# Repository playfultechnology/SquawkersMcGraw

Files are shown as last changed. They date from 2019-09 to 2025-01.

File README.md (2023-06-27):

# SquawkersMcGraw
Reverse engineering and remixing the Hasbro FurReal Friend "Squawkers McGraw" animatronic parrot
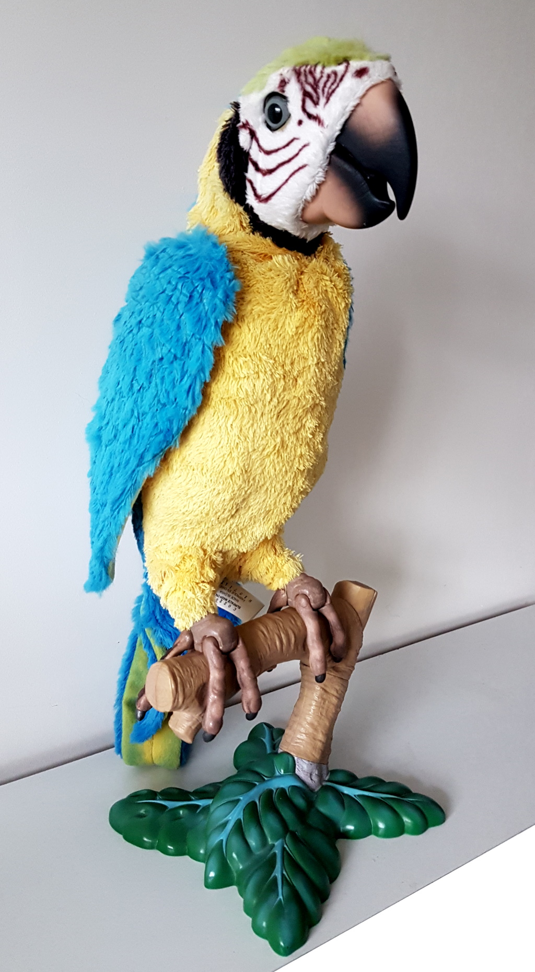
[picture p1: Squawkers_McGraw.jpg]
Squawkers McGraw Animatronic Parrot


## Internals
<table>
<tr>
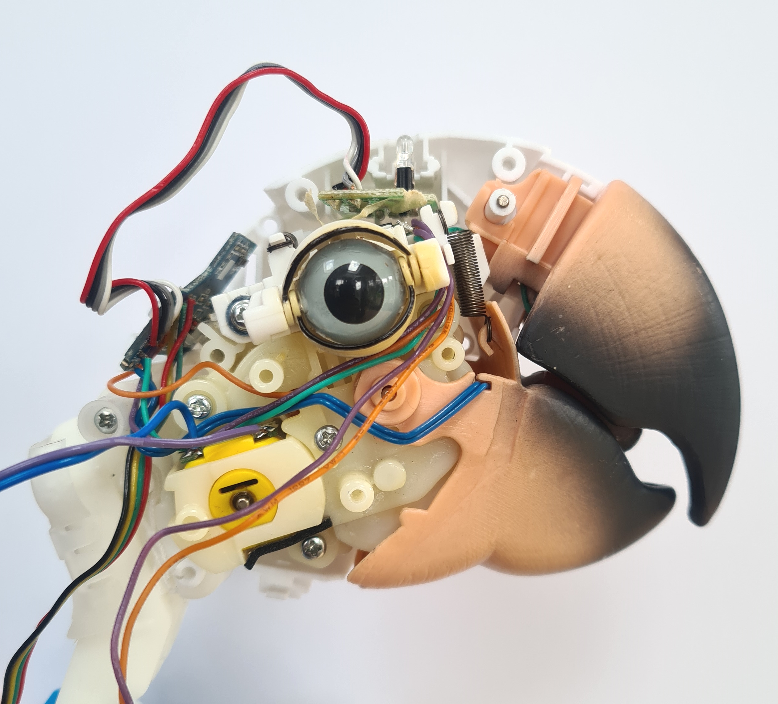
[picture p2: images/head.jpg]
Squawkers McGraw Head
<td></td>
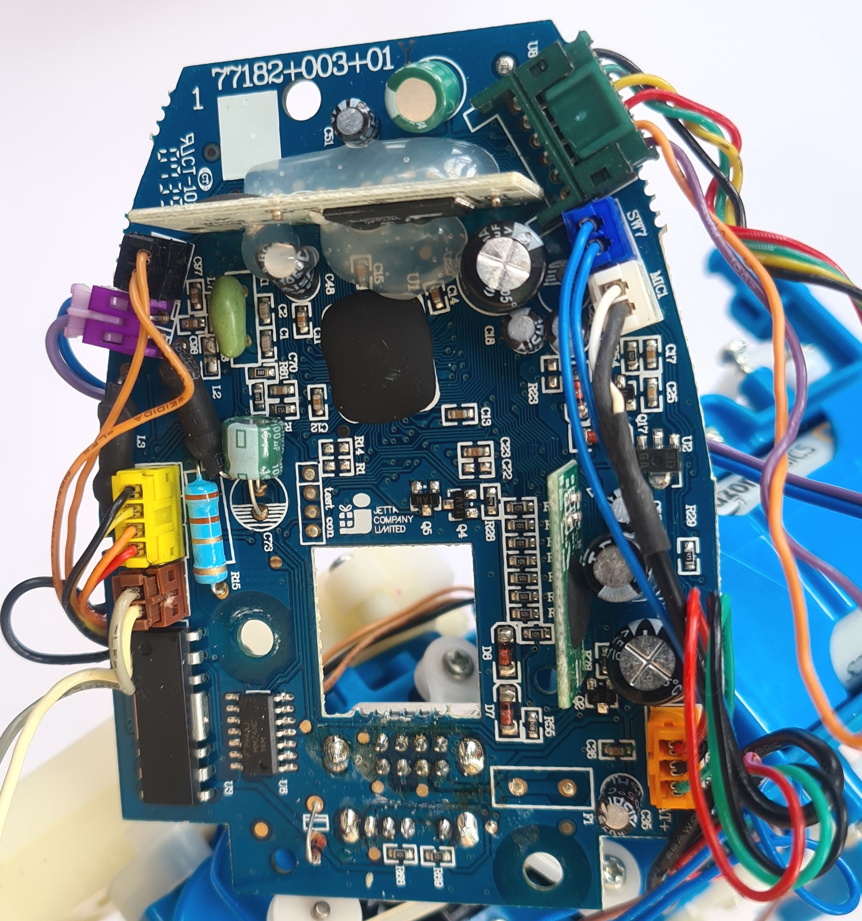
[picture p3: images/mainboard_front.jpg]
Squawkers McGraw Mainboard
<td></td>
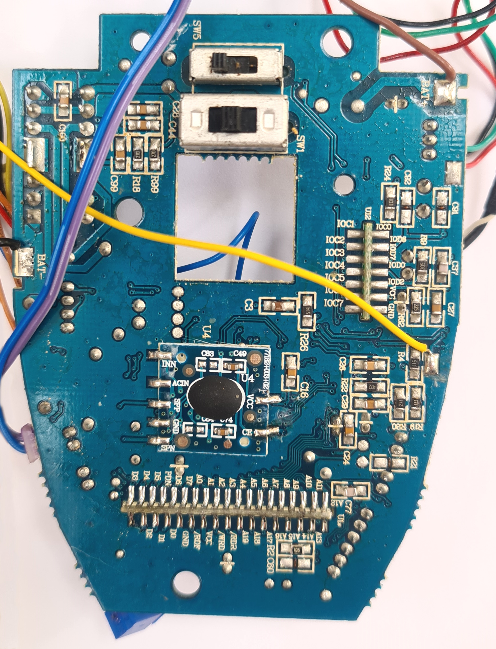
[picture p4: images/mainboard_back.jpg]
Squawkers McGraw Mainboard (back)
<td></td>
</tr>
</table>
The main control board in mounted in the middle of the parrot's back, with wires to the separate components located around the body as follows:

### Inputs
There are a variety of switches and sensor inputs, as follows:

- Light sensor), connected via Red, Black, Grey, White wires to a seperate control daughterboard located at the base of the head.
- Tongue switch (head), connected via 2x Blue wires (one ground).
- Eyelid limit switches - one is pressed when eyes are fully-open (2x Orange wires, one is ground), and one switch pressed when they are fully-closed (2x Purple wires, one is ground). When neither switch is pressed, eyes are in the neutral position.
- Leg switch, located on the left leg, is pressed at certain positions during the parrot's body movement. 

### Outputs
All the movements are controlled via only two DC hobby motors. By using a clever CAM system, reversing the direction of the motors can trigger different actuators. 
- Eyelid and mouth movement are both controlled from the one motor located in the head, connected via slightly thicker Blue and Purple wires.
- Wings and fully body tilt are controlled from a second motor, located at the hips, connected via White and Grey wire.

## Infrared Controller
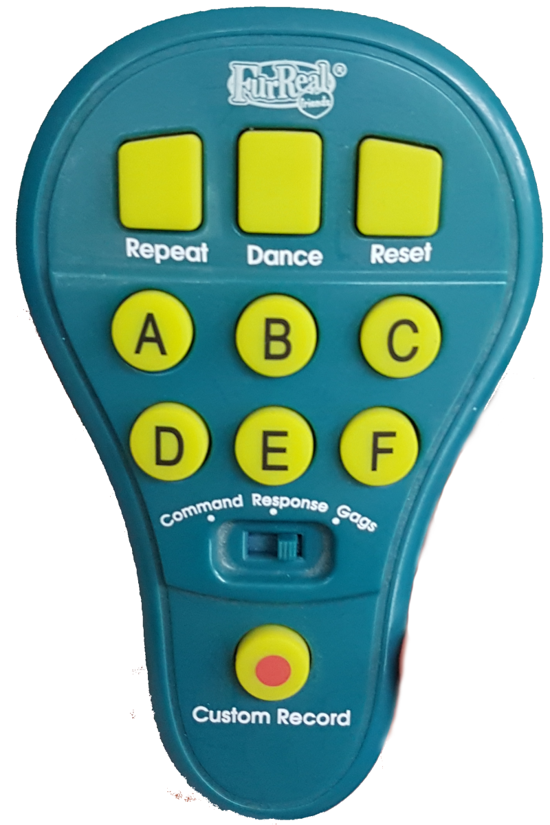
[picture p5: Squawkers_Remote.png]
Squawkers McGraw Contoller


The controller has a three position switch, three play mode buttons, 6 program buttons, and a custom record button. It appears to broadcast command strings using the common 38kHz carrier frequency. For a non-destructive method of controlling Squawkers McGraw, you can simply transmit these same command codes to trigger any of the built-in behaviours.

The following command strings were grabbed using an Arduino and the InfraRed signal analyser code described at https://www.patreon.com/posts/infrared-puzzle-28343366

### Response Mode
```
// Repeat Button
unsigned int repeatData[17] = {3000,3000,1000,2000,1000,2000,1000,2000,1000,2000,2000,1000,1000,2000,2000,1000,1000};

// Dance (same in every mode)
unsigned int danceData[17] = {3000,3000,1000,2000,2000,1000,1000,2000,2000,1000,2000,1000,1000,2000,2000,1000,1000};

// Reset (same in every mode)
unsigned int resetData[17] = {3000,3000,1000,2000,2000,1000,2000,1000,1000,2000,1000,2000,2000,1000,1000,2000,1000};

// Buttons
unsigned int aData[17] = {3000,3000,1000,2000,1000,2000,1000,2000,1000,2000,2000,1000,1000,2000,2000,1000,1000};
unsigned int bData[17] = {3000,3000,1000,2000,1000,2000,1000,2000,2000,1000,1000,2000,2000,1000,1000,2000,1000};
unsigned int cData[17] = {3000,3000,1000,2000,1000,2000,1000,2000,2000,1000,2000,1000,2000,1000,2000,1000,1000};
unsigned int dData[17] = {3000,3000,1000,2000,1000,2000,2000,1000,1000,2000,2000,1000,1000,2000,1000,2000,1000};
unsigned int eData[17] = {3000,3000,1000,2000,1000,2000,2000,1000,2000,1000,1000,2000,1000,2000,2000,1000,1000};
unsigned int fData[17] = {3000,3000,1000,2000,1000,2000,2000,1000,2000,1000,2000,1000,2000,1000,1000,2000,1000};

// Custom Record
unsigned int customRecordData[17] = {3000,3000,1000,2000,2000,1000,2000,1000,1000,2000,2000,1000,2000,1000,2000,1000,1000};
```
### Command Mode
```
// Repeat Button (same for Command and Gags)
unsigned int repeatData[17] = {3000,3000,1000,2000,2000,1000,1000,2000,1000,2000,1000,2000,2000,1000,2000,1000,1000};

// Dance (same in every mode)
unsigned int danceData[17] = {3000,3000,1000,2000,2000,1000,1000,2000,2000,1000,2000,1000,1000,2000,2000,1000,1000};

// Reset (same in every mode)
unsigned int resetData[17] = {3000,3000,1000,2000,2000,1000,2000,1000,1000,2000,1000,2000,2000,1000,1000,2000,1000};

// Buttons
unsigned int aData[17] = {3000,3000,1000,2000,1000,2000,1000,2000,1000,2000,2000,1000,2000,1000,1000,2000,1000};
unsigned int bData[17] = {3000,3000,1000,2000,1000,2000,1000,2000,2000,1000,1000,2000,2000,1000,2000,1000,1000};
unsigned int cData[17] = {3000,3000,1000,2000,1000,2000,2000,1000,1000,2000,1000,2000,1000,2000,1000,2000,1000};
unsigned int dData[17] = {3000,3000,1000,2000,1100,2000,2000,1000,1000,2000,2000,1000,1100,2000,2000,1000,1000};
unsigned int eData[17] = {3000,3000,1000,2000,1000,2000,2000,1000,2000,1000,1000,2000,2000,1000,1000,2000,1000};
unsigned int fData[17] = {3000,3000,1000,2000,1000,2000,2000,1000,2000,1000,2000,1000,2000,1000,2000,1000,1000};

// Custom Record [same as Response]
unsigned int customRecordData[17] = {3000,3000,1000,2000,2000,1000,2000,1000,1000,2000,2000,1000,2000,1000,2000,1000,1000};
```

### Gags Mode
```
// Repeat Button (same for Command and Gags)
unsigned int repeatData[17] = {3000,3000,1000,2000,2000,1000,1000,2000,1000,2000,1000,2000,2000,1000,2000,1000,1000};

// Dance (same in every mode)
unsigned int danceData[17] = {3000,3000,1000,2000,2000,1000,1000,2000,2000,1000,2000,1000,1000,2000,2000,1000,1000};

// Reset (same in every mode)
unsigned int resetData[17] = {3000,3000,1000,2000,2000,1000,2000,1000,1000,2000,1000,2000,2000,1000,1000,2000,1000};

// Buttons
unsigned int aData[17] = {3000,3000,1000,2000,1000,2000,1000,2000,1000,2000,2000,1000,2000,1000,2000,1000,1000};
unsigned int bData[17] = {3000,3000,1000,2000,1000,2000,1000,2000,2000,1000,2000,1000,1000,2000,1000,2000,1000};
unsigned int cData[17] = {3000,3000,1000,2000,1000,2000,2000,1000,1000,2000,1000,2000,1000,2000,2000,1000,1000};
unsigned int dData[17] = {3000,3000,1000,2000,1000,2000,2000,1000,1000,2000,2000,1000,2000,1000,1000,2000,1000};
unsigned int eData[17] = {3000,3000,1000,2000,1000,2000,2000,1000,2000,1000,1000,2000,2000,1000,2000,1000,1000};
unsigned int fData[17] = {3000,3000,1000,2000,2000,1000,1100,2000,1000,2000,1000,2000,1000,2000,1000,2000,1000};

// Custom Record
unsigned int customRecordData[17] = {3000,3000,1000,2000,2000,1000,1000,2000,1000,2000,1000,2000,1000,2000,1000,2000,1000};
```
## Hacking the Parrot
To completely customise the parrot's behaviour requires a more destructive modification - breaking the connections to the control board and instead wiring the inputs and outputs to a processor such as an Arduino, as follows:

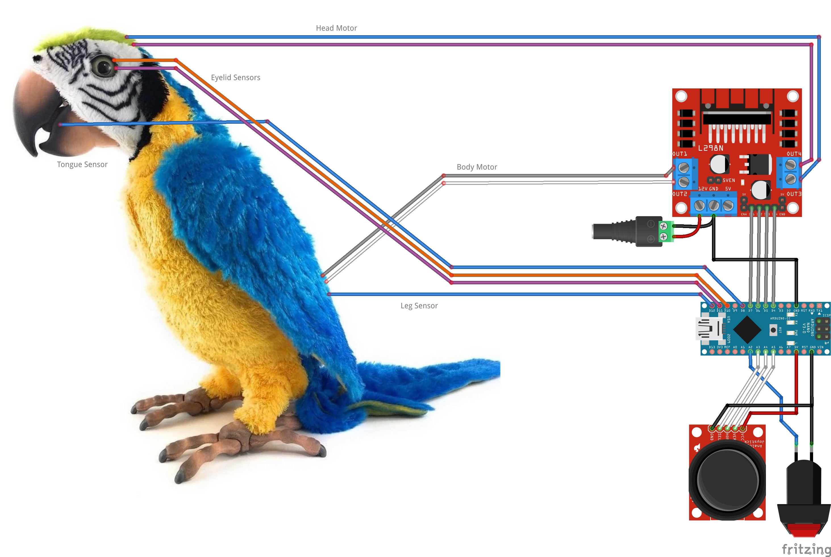
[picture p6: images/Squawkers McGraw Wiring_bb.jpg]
Squawkers McGraw Wiring


Note that each of the sensors illustrated actually consists of a pair of wires - one input signal, and one ground wire (with the controller having onboard INPUT_PULLUPs for when the inputs are not triggered). The code used to control such a modified controller is demonstrated in an Arduino .ino sketch in this repository.

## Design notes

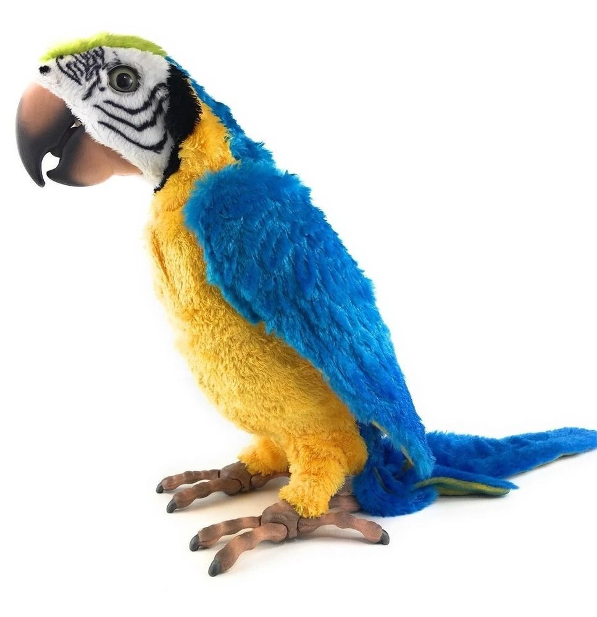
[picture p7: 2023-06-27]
images/squawkers.png

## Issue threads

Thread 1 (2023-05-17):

Diagram or Photo of Ardunio Connections to Squawkers boards

brad3d, 2023-05-17:
I saw you posted the Ardunio file for Squawkers control and the teardown images. Very cool work! I see you have the pinouts listed in the code. It would be great to get a diagram or photo of the Squawkers boards with where you connected the wires from the Arduino.

alastaira, 2023-05-18:
You can identify those connections from the coloured wires described in the readme: https://github.com/playfultechnology/SquawkersMcGraw

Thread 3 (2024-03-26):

Question re: Voltage of Motor Driver

thesavant42, 2024-03-26:
Firstly, amazing RE on the bird, great work! In the fritzing diagram I see that the motor driver is configured for 12v. Is this intentional? I want to make sure before I risk making chicken nuggets.

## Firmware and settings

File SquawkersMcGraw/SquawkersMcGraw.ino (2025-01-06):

/**
 * "Squawkers McGraw" Animatronic Controller
 * Copyright (c) 2023 Playful Technology 
 */

// INCLUDES
// For debouncing button input. See https://github.com/LennartHennigs/Button2
#include "Button2.h"
#include "DYPlayerArduino.h"
#include <U8g2lib.h>
// using the ESP32 built-in bluetooth, so no need for serial Bluetooth connection to, e.g. HC-05
#include "BluetoothSerial.h"

// ENUMS
// Define the states through which the parrot's eyes and body moves
enum EyeState { Open, Closing, Neutral, Closed, Opening };
enum BodyState { bdyNeutral, bdyFlapWingsHeadDown, bdyLookRightHeadUp, bdyHeadLeft, bdyNeutralFlapWing };

// CONSTANTS
// Outpin pins
// TP6612 motor driver has 3 pins per channel. IN1/IN2/PWM
byte bodyMotorPins[] = {27, 26, 25}; // White/Grey wires
byte headMotorPins[] = {12, 14, 13}; // Blue/Purple wires
// Sensor pins
const byte numSensors = 4;
const byte tonguePin = 36; // Blue wire to head
const byte eyesClosedPin = 39; // Orange wire
const byte eyesOpenPin = 34; // Purple wire
const byte legPin = 35; // Blue wire
const byte sensorPins[numSensors] = {tonguePin, eyesClosedPin, eyesOpenPin, legPin};

const byte audioRxPin = 16, audioTxPin = 17;

// GLOBALS
Button2 sensors[numSensors];
#ifdef ESP32
  BluetoothSerial BTSerial;
#else
// Initialize Serial2 for Bluetooth communication on GPIO 16 (Rx) and GPIO 17 (Tx)
// HardwareSerial BTSerial(2);  // Use Serial2 for Bluetooth
#endif
// Initialize the U8g2 library with I2C connection on GPIO 32 (SDA) and GPIO 33 (SCL)
U8G2_SSD1306_128X32_UNIVISION_F_HW_I2C u8g2(U8G2_R0, /* reset=*/ U8X8_PIN_NONE, /* clock=*/ 33, /* data=*/ 32);
// Keep track of current position
int8_t lastBodyMovement = 0;
bool wingsOpen = true;
EyeState eyeState = EyeState::Neutral;
DY::Player player(&Serial2);

void setup() {
  Serial.begin(115200);
  delay(1000);
  Serial.println(__FILE__ __DATE__);

  // Initialize the OLED display
  u8g2.begin();
  u8g2.clearBuffer();
  u8g2.setFont(u8g2_font_simple1_tr); // Choose a font size that fits your display
  
  Serial2.begin(9600, SERIAL_8N1, audioRxPin, audioTxPin);
  player.begin();
  player.setVolume(31);
  player.playSpecified(2);

  // Initialize Bluetooth Serial
  #ifdef ESP32
    // Built-in Bluetooth interface needs only advertised name
    BTSerial.begin("SquawkersMcGraw");
  #else
    // If using an external Bluetooth module (e.g. HC-05), specify the parameters
    // of the serial interface to it - baud rate, Rx, Tx pin
    BTSerial.begin(9600, SERIAL_8N1, 8, 9);
  #endif

  // Display welcome message on the OLED
  u8g2.drawStr(0, 10, "Waiting for BT data...");
  u8g2.sendBuffer();

  // Motors
  for(int i=0; i<3; i++){
    pinMode(headMotorPins[i], OUTPUT);  
    pinMode(bodyMotorPins[i], OUTPUT);
  }
  // Set default PWM speed for motor movements
  analogWrite(headMotorPins[2], 255);
  analogWrite(bodyMotorPins[2], 255);
  
  // Sensors
  for(int i=0; i<numSensors; i++){
    pinMode(sensorPins[i], INPUT_PULLUP);
    sensors[i].begin(sensorPins[i]);
    sensors[i].setDebounceTime(1);
    sensors[i].setChangedHandler(sensorChanged);
  }

  openEyes();
  delay(500);
  calibrateBody();
}

void sensorChanged(Button2& sensor) {
  Serial.print("Sensor changed: ");
  if(sensor.getPin() == tonguePin) {
    Serial.println(sensor.isPressed() ? "Tongue pressed" : "Tongue released");    
  }
  else if(sensor.getPin() == legPin) {
    Serial.println(sensor.isPressed() ? "Leg pin pressed" : "Leg pin released");
    stopMoving();
  }
  else if(sensor.getPin() == eyesOpenPin || sensor.getPin() == eyesClosedPin) {
    eyeState = getEyeState();
  }

  // DEBUG - print current status of all sensors  
  //reportSensorValues();
  // TESTING!
  // For stepping through head motor movement
  //stopEyes();
}


EyeState getEyeState(){
    if(digitalRead(eyesClosedPin) && !digitalRead(eyesOpenPin)){
      Serial.println("Eyes Open");
      return EyeState::Open;
    }
    else if(digitalRead(eyesClosedPin) && digitalRead(eyesOpenPin)){
      Serial.println("Eyes Neutral");
      return  EyeState::Neutral;
    }
    else if(!digitalRead(eyesClosedPin) && digitalRead(eyesOpenPin)){
      Serial.println("Eyes Closed");
      return EyeState::Closed;
    }
    else {
      // Default
      Serial.print("ERROR: Could not determine eye state");
      return EyeState::Neutral;
    }
}


/**
 * Open eyes is the same head movement as open mouth
 */
void openEyes(){
  Serial.println(F("Open Eyes"));  
  u8g2.drawStr(0, 10, "Opening eyes...");
  u8g2.sendBuffer();

  unsigned long now = millis();
  while((millis() - now < 200) && getEyeState() != EyeState::Open){
    digitalWrite(headMotorPins[0], LOW);
    digitalWrite(headMotorPins[1], HIGH);
    analogWrite(headMotorPins[2], 128);
  }
  /*
  switch(eyeState){
    case EyeState::Neutral:
      // Open eyes until closed pin is no longer pressed
      while((millis() - now < 250) && getEyeState() != EyeState::Open){
        digitalWrite(headMotorPins[0], HIGH);
        digitalWrite(headMotorPins[1], LOW);
        digitalWrite(headMotorPins[2], 64);
        delay(10);
        stopEyes();
      }
      break;
    case EyeState::Closed:
      // Open eyes until open pin is pressed
      while((millis() - now < 250) && getEyeState() != EyeState::Neutral){
        digitalWrite(headMotorPins[0], HIGH);
        digitalWrite(headMotorPins[1], LOW);
        digitalWrite(headMotorPins[2], 64);
        delay(10);
        stopEyes();
      }
      break;
    default:
      break;
  }
*/
  stopEyes();
}
void closeEyes(){
  Serial.println(F("Close Eyes"));  
  u8g2.drawStr(0, 10, "Closing Eyes...");
  u8g2.sendBuffer();
  unsigned long now = millis();
  /*
  while((millis() - now < 250) && getEyeState() != EyeState::Closed){
    digitalWrite(headMotorPins[0], HIGH);
    digitalWrite(headMotorPins[1], LOW);
    digitalWrite(headMotorPins[2], 64);
  }
  */
  switch(eyeState){
    case EyeState::Neutral:
      // Close eyes until open pin is no longer pressed
      while((millis() - now < 250) && getEyeState() != EyeState::Closed){
        digitalWrite(headMotorPins[0], HIGH);
        digitalWrite(headMotorPins[1], LOW);
        analogWrite(headMotorPins[2], 64);
      }
      break;
    case EyeState::Open:
      // Close eyes until closed pin is pressed
      while((millis() - now < 250) && getEyeState() != EyeState::Neutral){
        digitalWrite(headMotorPins[0], HIGH);
        digitalWrite(headMotorPins[1], LOW);
        analogWrite(headMotorPins[2], 64);
      }
      break;
    default:
      break;
  }

  stopEyes();
}
void stopEyes(){
  digitalWrite(headMotorPins[0], LOW);
  digitalWrite(headMotorPins[1], LOW);
  digitalWrite(headMotorPins[2], LOW);
}
/**
/* Note: BLINKING is the opposite of TALKING
 */
void blink(){
  Serial.print(F("Blinking"));  
  u8g2.drawStr(0, 10, "Blinking...");
  u8g2.sendBuffer();
  unsigned long now = millis();
  // Close eyes all the way
  while((millis() - now < 200) && (eyeState != EyeState::Closed)){
    digitalWrite(headMotorPins[0], HIGH);
    digitalWrite(headMotorPins[1], LOW);
    digitalWrite(headMotorPins[2], 255);
  }
  // Open eyes all the way
  while((millis() - now < 200) && (eyeState != EyeState::Open)){
    digitalWrite(headMotorPins[0], LOW);
    digitalWrite(headMotorPins[1], HIGH);
    digitalWrite(headMotorPins[2], 192);
  }
  stopEyes();
}

// Spinning head motor in one direction opens mouth
// (will also open eyes)
void openMouth(){
  Serial.println(F("Open Mouth"));
  u8g2.drawStr(0, 10, "Opening Mouth");
  u8g2.sendBuffer();  
  digitalWrite(headMotorPins[0], LOW);
  digitalWrite(headMotorPins[1], HIGH);
  analogWrite(headMotorPins[2], 255);
  digitalWrite(LED_BUILTIN, HIGH);
  player.playSpecified(1);
}
// Mouth is sprung so will automatically close when head motor is unpowered
void closeMouth(){
  Serial.println(F("Close Mouth"));
  u8g2.drawStr(0, 10, "Closing Mouth...");
  u8g2.sendBuffer();
  digitalWrite(headMotorPins[0], LOW);
  digitalWrite(headMotorPins[1], LOW);
  analogWrite(headMotorPins[2], 0);
  digitalWrite(LED_BUILTIN, LOW);
}

void talk(){
  Serial.print(F("Talking"));
  player.playSpecified(3);
  delay(250);
  // Open eyes first....
  openEyes();
  unsigned long now = millis();
  EyeState previousEyeState = eyeState;
  // Open mouth (and eyes)
  while((millis() - now < 100)){
    digitalWrite(headMotorPins[0], LOW);
    digitalWrite(headMotorPins[1], HIGH);
    analogWrite(headMotorPins[2], 255);
  }
  // Close mouth again until returned to previous eye state
  while((millis() - now < 200 && eyeState != previousEyeState)){
    digitalWrite(headMotorPins[0], HIGH);
    digitalWrite(headMotorPins[1], LOW);
    analogWrite(headMotorPins[2], 0);
    for(int i=0; i<numSensors; i++){ sensors[i].loop(); }
  }
  // Stop
  digitalWrite(headMotorPins[0], LOW);
  digitalWrite(headMotorPins[1], LOW);
  analogWrite(headMotorPins[2], 0);

}

// Cycle through movement patterns in specified direction
//<0   1>
//Mouth Open (no sensor) <> Eyes Open <> Neutral Eyes <> Eyes Closed <> Eyes straining to be _really_ closed (from this state, 0 goes back to OPEN though, not neutral....)

void moveHead(int dir=0){
  Serial.println(F("Move head"));
  player.playSpecified(4);
  delay(250);
  u8g2.drawStr(0, 10, "Moving...");
  u8g2.sendBuffer();
  digitalWrite(headMotorPins[0], dir);
  digitalWrite(headMotorPins[1], 1-dir);
  analogWrite(headMotorPins[2], 128);
}
void stopHead(){
  Serial.println(F("Stopping head"));
  u8g2.drawStr(0, 10, "Stopping...");
  u8g2.sendBuffer();
  digitalWrite(headMotorPins[0], LOW);
  digitalWrite(headMotorPins[1], LOW);
  analogWrite(headMotorPins[2], 0);
}
// Move the body so we know the position it ends in
void calibrateHead(){
  unsigned long now = millis();
  do { 
    moveHead(1);
    delay(10);
    stopHead();
    for(int i=0; i<numSensors; i++){ sensors[i].loop(); }
    }
  while((millis() - now < 1000 && eyeState != EyeState::Neutral));
}
/*
A <- MOVEMENT A <-Slight Wiggle -> MOVEMENT B -> B -> B
|         ^
\----------
*/
// Cycle through movement patterns in specified direction
void moveBody(int dir=0){
  Serial.println(F("Move"));
  u8g2.drawStr(0, 10, "Moving...");
  u8g2.sendBuffer();
  digitalWrite(bodyMotorPins[0], dir);
  digitalWrite(bodyMotorPins[1], 1-dir);
  analogWrite(bodyMotorPins[2], 255);
  lastBodyMovement = dir;
  wingsOpen = dir;
}
// Stop all body movement
void stopMoving(){
  Serial.println(F("Stop"));  
  u8g2.drawStr(0, 10, "Stopping...");
  u8g2.sendBuffer();
  digitalWrite(bodyMotorPins[0], LOW);
  digitalWrite(bodyMotorPins[1], LOW);
  analogWrite(bodyMotorPins[2], 0);
}
// To flap wings, we move body in the opposite direction to last time it was moved
void flap(){
  moveBody(1-lastBodyMovement);
}
// These are more limited versions of flap()
void shutWings(){
  if(wingsOpen){
    moveBody(0);
  }
}
// These are more limited versions of flap()
void openWings(){
  if(!wingsOpen){
    moveBody(1);
  }
}
// Move the body so we know the position it ends in
void calibrateBody(){
  moveBody(0);
}

void reportSensorValues(){
  // tonguePin, eyesClosedPin, eyesOpenPin, legPin
  for(int i=0; i<numSensors; i++){
    Serial.print(digitalRead(sensorPins[i]));
    Serial.print(i==numSensors-1 ? "\r\n" : ",");
  }
}

void loop() {
  // Note that responding to digital button inputs and handling sensor changes
  // are done in callback methods above (btnPressed, btnReleased, and sensorChanged)
  // so are not in loop()
  // For debugging, we will also accept commands sent over the Serial connection
  // Read any input
  char command;
  bool cmdReceived = false;
  if(Serial.available() > 0){
    // Read any single character sent
    command = Serial.read();
    cmdReceived = true;
  }
  // Check if data is available on Bluetooth
  else if(BTSerial.available()) {
    command = BTSerial.read();
    cmdReceived = true;
  }
  if(cmdReceived){
    switch(command){
      case '!':
        reportSensorValues();
        break;
      case '$':
        calibrateHead();
        break;
      case 'f':
        flap();
        break;
      case 'b':
        blink();
        break;
      case 'z':
        moveBody(0);
        break;
      case 'x':
        moveBody(1);
        break;
      case 'o':
        openWings();
        break;
      case 's':
        shutWings();
        break;
      case 't':
        talk();
        break;
      case '1':
        moveHead(0);
        break;
      case '2':
        moveHead(1);
        break;  
      case '3':
        openMouth();
        delay(100);
        closeMouth();
        break;
      case '4':
        blink();
        break;
      case '5':
        openEyes();
        break;
      case '6':
        closeEyes();
        break;
      case '7':
        moveBody(0);
        break;
      case '8':
        moveBody(1);
        break;
    }
  }
  for(int i=0; i<numSensors; i++){ sensors[i].loop(); }
}

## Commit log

2023-04-18 Create SquawkersMcGraw.ino
    Added Arduino code
2023-06-24 Update SquawkersMcGraw.ino
    Major revision to codebase - now incorporates sensors to allow for three eye states, support for controller and serial command input.
2023-06-27 Added Wiring diagram
    [Squawkers McGraw Wiring.fzz]
2023-06-27 Updated wiring
    [Squawkers McGraw Wiring.fzz]
2024-04-05 Update SquawkersMcGraw.ino
    Corrected enum collision between Body and Eye neutral state
    [SquawkersMcGraw.ino]
